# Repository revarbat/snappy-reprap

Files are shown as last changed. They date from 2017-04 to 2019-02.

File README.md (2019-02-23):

Snappy Full Rendering

Snappy-Reprap 3
===============

A parametric design for a cheap self-replicating 3D printer (reprap) that snaps together to minimize screws and non-printed parts.

Important Links:

What                 | URL
-------------------- | -------------------------------------------------------
GitHub Repository    | https://github.com/revarbat/snappy-reprap
Project Wiki         | https://github.com/revarbat/snappy-reprap/wiki/v3.0-Home
Bill of Materials    | https://github.com/revarbat/snappy-reprap/wiki/v3.0-BOM
How to Assemble      | https://github.com/revarbat/snappy-reprap/wiki/v3.0-Assembly
RepRap.org Wiki Page | http://reprap.org/wiki/Snappy
Dev Forum            | https://groups.google.com/forum/#!forum/snappy-reprap-dev



Generating STL Files
====================
For all platforms, you will need to have OpenSCAD installed. You can download OpenSCAD from their website at [http://www.openscad.org](http://www.openscad.org)

To insure the best fit of parts, print the [slop calibrator STL file](https://github.com/revarbat/snappy-reprap/blob/master/STLs/slop_calibrator_parts.stl) on the parent printer using the desired print settings. Then update the printer_slop variable in the config.scad file on line 130. Then proceed to generating STL files.

OS X:
-----
Under OS X, you'll need to make sure you have the Xcode command-line tools installed first.  You can get them by installing Xcode from the App Store.

You shouldn't need to change the Makefile.  It should set $OPENSCAD as:
```
OPENSCAD=/Applications/OpenSCAD.app/Contents/MacOS/OpenSCAD
```

To generate the STL model files, open a terminal to the snappy-reprap directory and type:
```
make
```

Linux:
------
Under Linux, you will need to edit the Makefile, and change $OPENSCAD to:
```
OPENSCAD=openscad
```
To generate the STL model files, open a terminal to the snappy-reprap directory and type:
```
make
```

Windows:
--------
Under Windows, you'll probably have to open and compile each `*_parts.scad` file individually and manually export the STL files.

You _might_ be able to run the makefile under CygWin, if you set $OPENSCAD to something like:
```
OPENSCAD="/Program Files/OpenSCAD/openscad.exe"
```

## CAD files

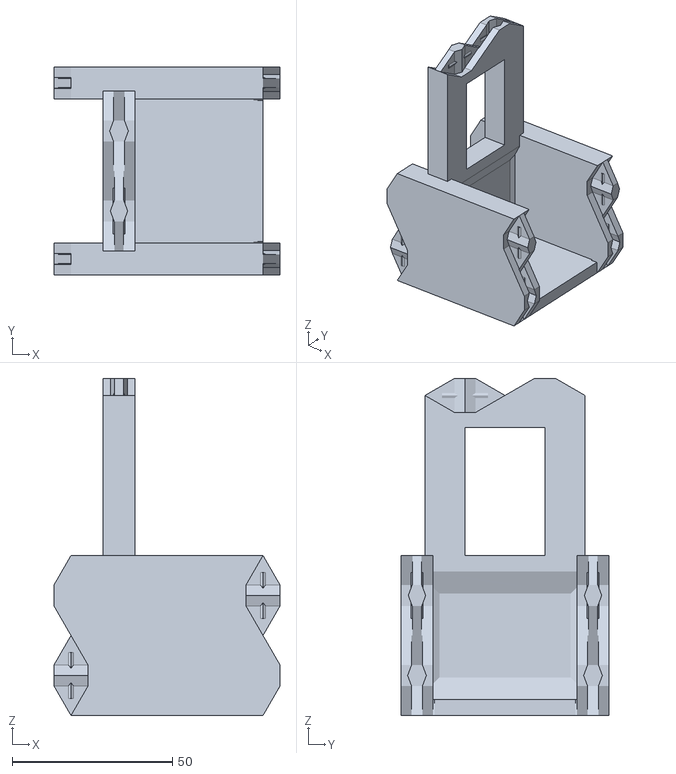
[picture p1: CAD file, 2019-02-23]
STLs/rail_z_endcap_parts.stl
70.6 x 65.0 x 105.3

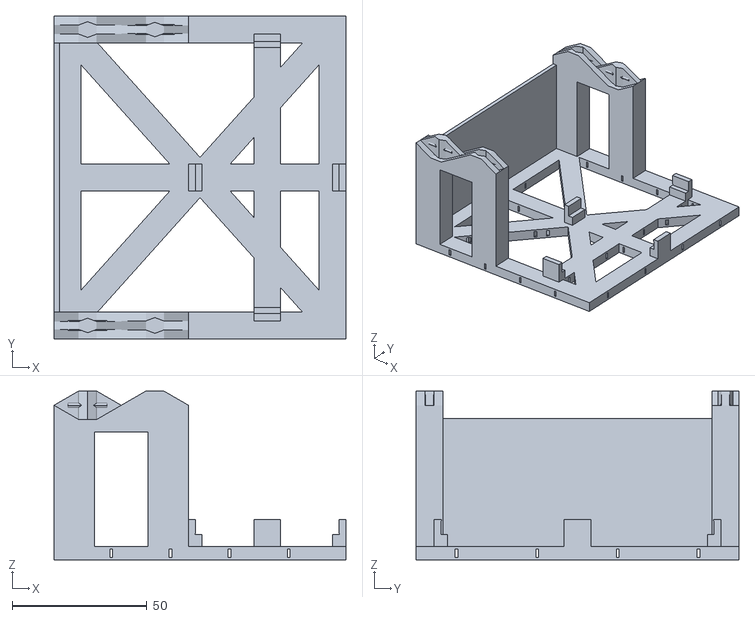
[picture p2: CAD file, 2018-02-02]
STLs/ramps_mount_parts.stl
108.5 x 120.0 x 62.8

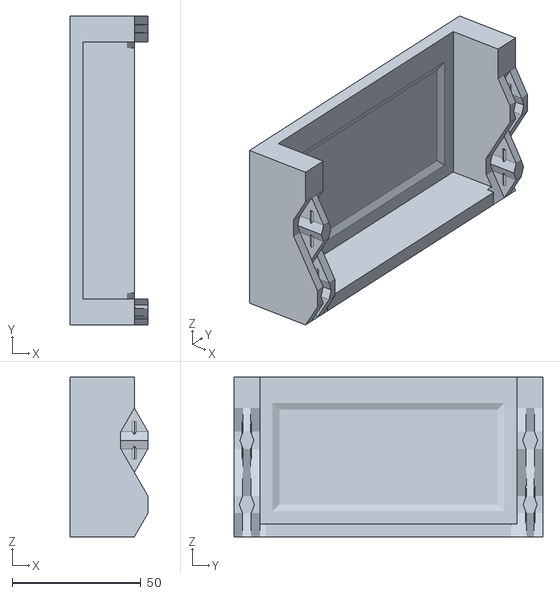
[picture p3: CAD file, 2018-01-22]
STLs/rail_y_endcap_parts.stl
30.3 x 120.0 x 62.0

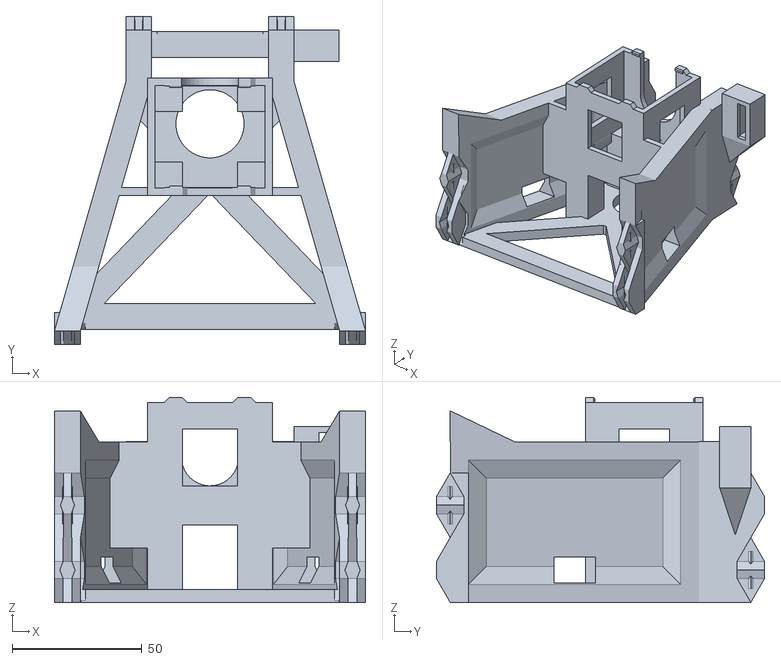
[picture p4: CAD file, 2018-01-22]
STLs/z_base_parts.stl
120.0 x 126.6 x 79.1

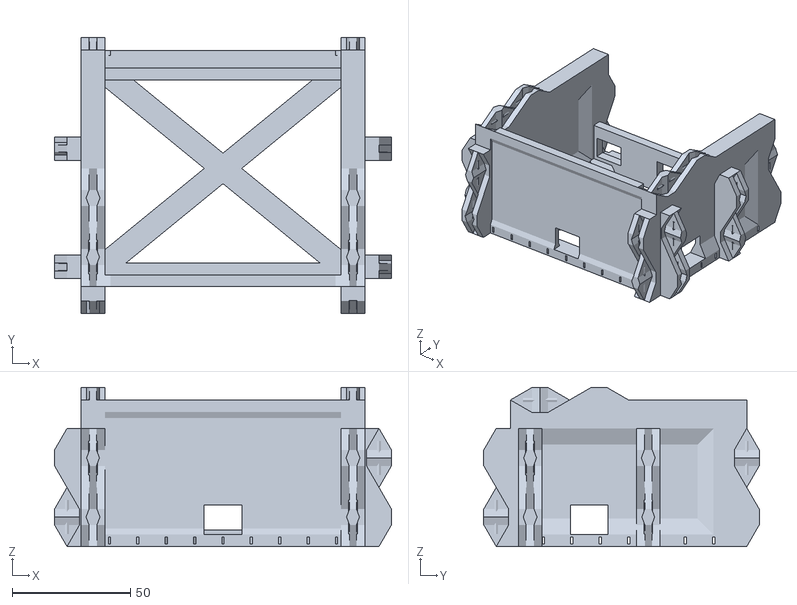
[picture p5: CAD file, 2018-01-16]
STLs/yz_joiner_parts.stl
142.6 x 116.6 x 67.3

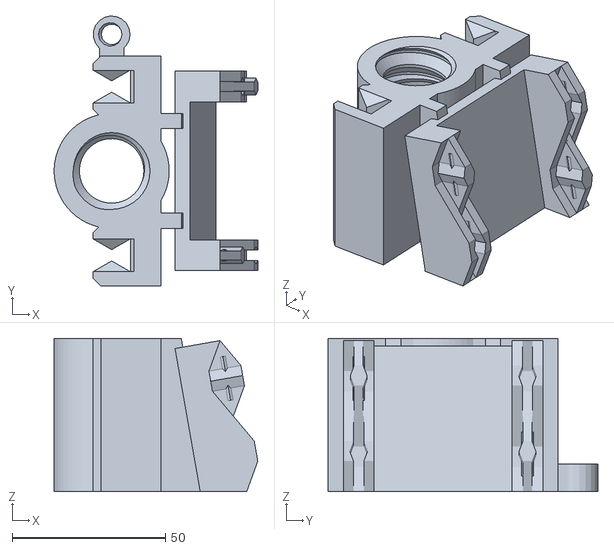
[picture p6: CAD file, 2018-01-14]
STLs/z_sled_parts.stl
66.3 x 88.0 x 50.0

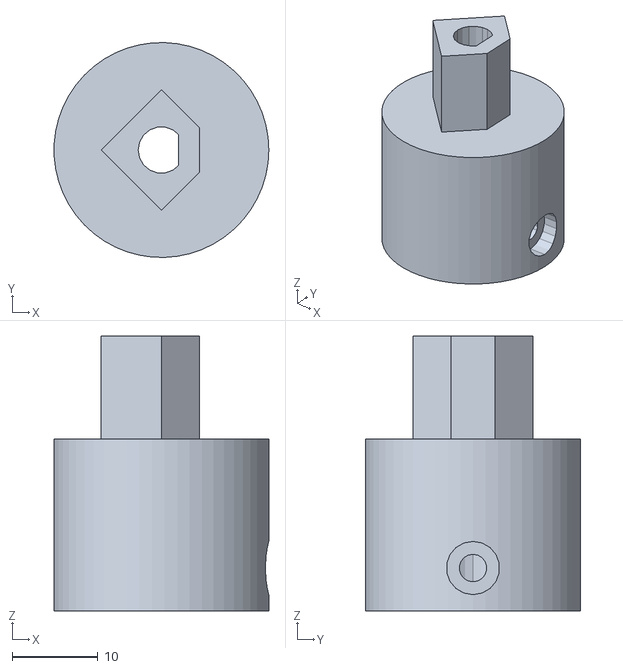
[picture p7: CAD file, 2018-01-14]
STLs/lifter_coupler_parts.stl
25.0 x 25.0 x 32.0

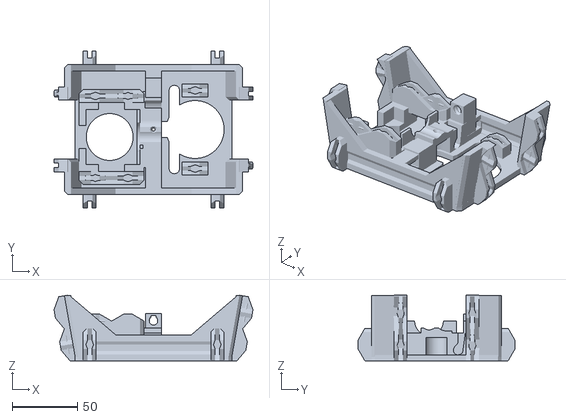
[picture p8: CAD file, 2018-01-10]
STLs/jhead_platform_parts.stl
152.8 x 120.6 x 50.5

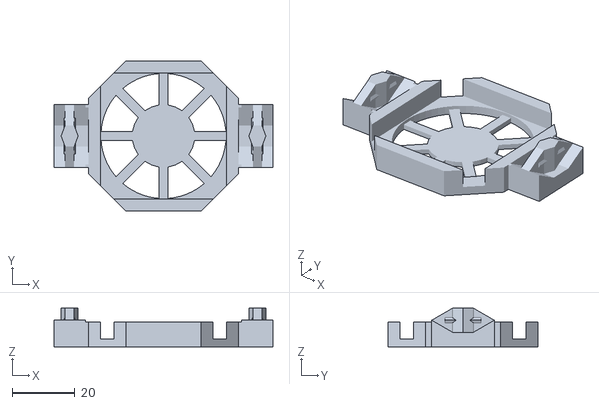
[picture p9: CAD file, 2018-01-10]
STLs/extruder_fan_clip_parts.stl
70.0 x 48.0 x 12.3

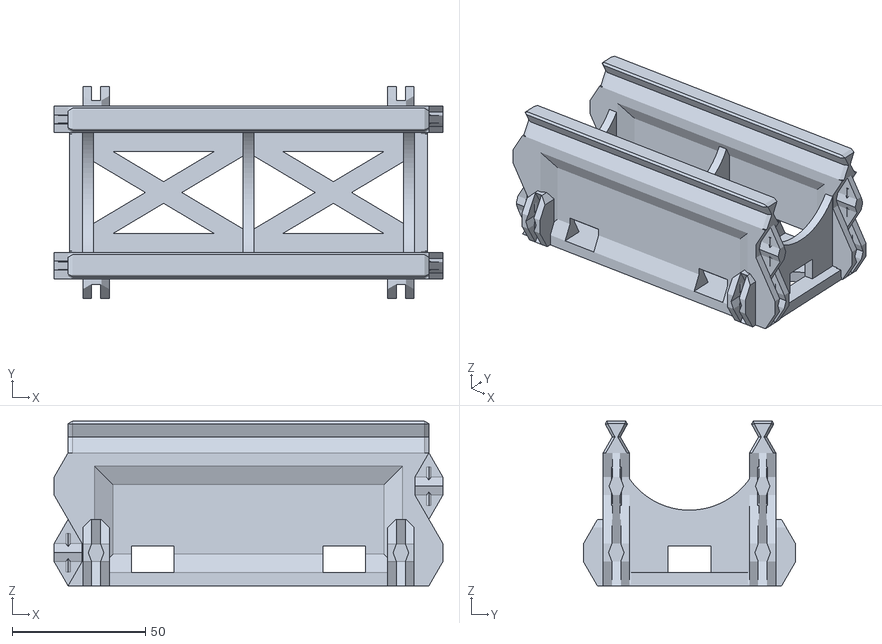
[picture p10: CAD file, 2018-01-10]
STLs/z_rail_parts.stl
146.2 x 79.8 x 62.0

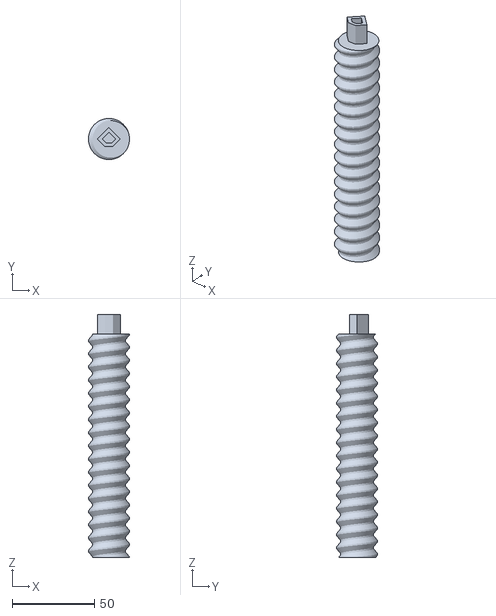
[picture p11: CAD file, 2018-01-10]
STLs/lifter_rod_parts.stl
25.0 x 25.0 x 147.8

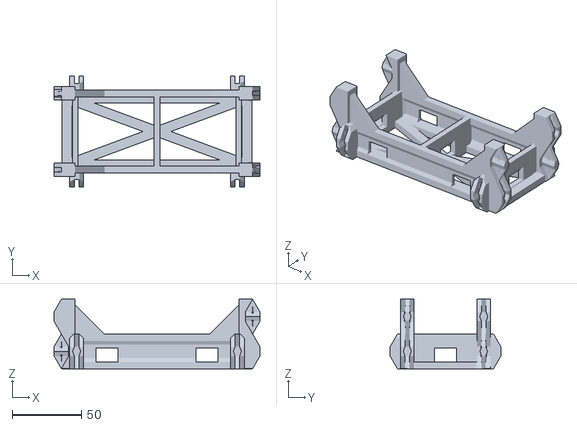
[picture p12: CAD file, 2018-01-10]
STLs/bridge_segment_parts.stl
148.3 x 79.8 x 50.0

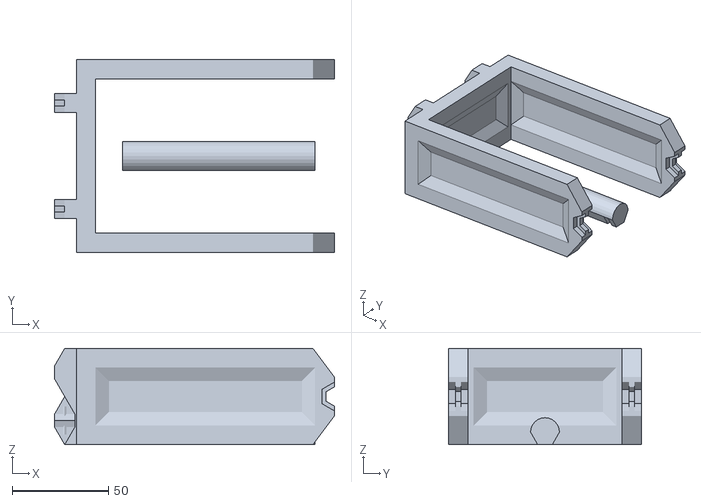
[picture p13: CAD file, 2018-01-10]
STLs/spool_holder_parts.stl
145.3 x 100.0 x 50.0

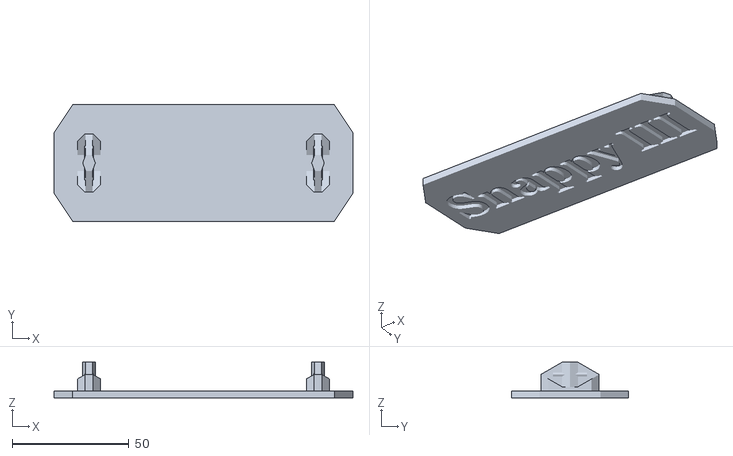
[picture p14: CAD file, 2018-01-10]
STLs/snappy_logo_parts.stl
128.0 x 50.0 x 15.3

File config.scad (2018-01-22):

snappy_version = 2.000;


// 0 = Thinning Walls (Thin in the middle, thick at edges.  Prettier smooth solid walls.)
// 1 = Corrugated closed walls. (Zig-zagged solid walls. Less shrinkage stress.)
// 2 = Crossbeam walls. (Open sparse struts. Far less shrinkage stress. Recommended.)
wall_styling = 0;


platform_length = 100.0;  // mm.  Must be a multiple of rack_tooth_size.
platform_width  = 150.0;  // mm
platform_height =  40.0;  // mm
platform_thick  =   5.0;  // mm

rail_length     = 136.0;  // mm  Should match lifter_rod_length
rail_height     =  50.0;  // mm
rail_thick      =   5.0;  // mm

motor_rail_length = 128.0; // mm

groove_angle    =  30;   // degrees
groove_height   =  12;   // mm

joiner_angle    =  30;   // degrees
joiner_width    =  10;   // mm

rack_tooth_size     = 10/3;    // mm per tooth.
rack_height         = 15;    // mm
gear_base           = 10;    // mm
gear_teeth          = 24;
set_screw_size      =  3;    // mm size of set screw in drive gears, couplers, etc
motor_length        = 39.25; // mm length of NEMA17 motor.
motor_shaft_size    =  5;    // mm diameter of NEMA17 motor shaft.
motor_shaft_length  = 20;    // mm length of exposed NEMA17 motor shaft.
motor_shaft_flatted = true;  // Is motor shaft keyed? (RECOMMENDED)

lifter_rod_diam     =  25; // mm
lifter_rod_pitch    =   8; // mm lift per revolution
lifter_rod_length   = 136; // mm. Must be a multiple of lifter_rod_pitch
lifter_rod_angle    =  50; // degrees tooth face angle
lifter_tang_length  =  12; // mm
lifter_tang_width   =   5; // mm
lifter_coupler_len  =  20; // mm

adjust_screw_diam   =  8.0; // mm
adjust_screw_pitch  =  3.0; // mm
adjust_screw_length = 30.0; // mm
adjust_screw_angle  = 50.0; // mm
adjust_screw_knob_d = 12.0; // mm
adjust_screw_knob_h =  5.0; // mm

// Mechanical endstop bare microswitch.
endstop_hole_spacing =  9.5; // mm
endstop_hole_inset   =  8.0; // mm
endstop_hole_hoff    = 10.0; // mm
endstop_click_voff   =  3.0; // mm
endstop_screw_size   =  2.5; // mm
endstop_length       = 19.8; // mm
endstop_thick        =  6.5; // mm
endstop_depth        = 10.0; // mm

// Standard Mk2b Heated Build Platform from RepRapDiscount.com
hbp_width       = 215;   // mm
hbp_length      = 215;   // mm
hbp_hole_width  = 208.5; // mm
hbp_hole_length = 208.5; // mm
hbp_screwsize   =   3;   // mm

// Standard 200mm square borosilicate glass build platform
glass_width     = 200;   // mm
glass_length    = 214;   // mm
glass_thick     =   3;   // mm
//glass_thick     =   4.6;   // mm  3mm glass and 1.6mm heated bed.  Print supports in ABS.

// Cable chain dimensions
cable_chain_height = 15;  // mm
cable_chain_width  = 25;  // mm
cable_chain_length = 26;  // mm
cable_chain_pivot  =  5;  // mm
cable_chain_bump   =  1.5;  // mm
cable_chain_wall   =  3.25;  // mm

spool_holder_length = 140.0;  // mm

bridge_arch_angle   =  10.0;  // degrees

jhead_vent_span     =  20.0;  // mm
jhead_barrel_diam   =  16.0;  // mm
jhead_shelf_thick   =   4.8;  // mm
jhead_groove_thick  =   4.6;  // mm
jhead_groove_diam   =  12.0;  // mm
jhead_cap_height    =   8.2;  // mm
jhead_cap_diam      =  12.0;  // mm

extruder_thick       =   5.0;  // mm
extruder_shaft_len   =  25.0;  // mm
extruder_drive_diam  =  12.5;  // mm

/*
// 626 bearing
extruder_idler_diam  =  19.0;  // mm
extruder_idler_axle  =   6.0;  // mm
extruder_idler_width =   6.0;  // mm
*/

/*
// SAE bearing 5/8"OD x 1/4"ID x 1/5"W
extruder_idler_diam  =  15.9;  // mm
extruder_idler_axle  =   6.3;  // mm
extruder_idler_width =   5.0;  // mm
*/

// 686 bearing
extruder_idler_diam  =  13.0;  // mm
extruder_idler_axle  =   6.0;  // mm
extruder_idler_width =   5.0;  // mm

extruder_fan_size    =  40.0;  // mm
extruder_fan_thick   =  10.0;  // mm

cooling_fan_size     =  40.0;  // mm
cooling_fan_thick    =  10.0;  // mm
cooling_duct_height  =  18.0;  // mm

filament_diam        =   1.75; // mm

// This is the slop needed to make parts fit more exactly, and might be
// printer and slicer dependant.  Printing a slop calibration block should
// help dial this setting in for your printer.
printer_slop = 0.20;  // mm
gear_backlash = 0;  // mm



// Commonly used derived values.  Don't change these.
pi = 3.141592653589793236+0.0;
extruder_length = motor_rail_length;
shaft_clear = max(0, motor_shaft_length - (rack_height + gear_base));
rail_offset = shaft_clear + platform_thick + rack_height/2 + 2.0;
rail_spacing = platform_width - joiner_width*4 - 10;
rail_width = rail_spacing + joiner_width*2;
rack_base = rail_offset - platform_thick + groove_height/2 - rack_height;
motor_mount_spacing = 43 + joiner_width + 10;
side_mount_spacing = motor_rail_length - 10*2;
platform_z = rail_height + groove_height + rail_offset;
cantilever_length = (motor_rail_length + 2*platform_length - 2*rail_height - extruder_length - groove_height)/2;
motor_top_z = rail_height + groove_height - rack_height/2 - gear_base - 2;
lifter_tooth_depth = lifter_rod_pitch / 3.2;
z_joiner_spacing = lifter_rod_diam + 20 + joiner_width;
z_base_height = 2*platform_z + glass_thick + 12 + 10 - rail_height - groove_height;
adjust_thread_depth = adjust_screw_pitch/3.2;
drive_gear_diam = (gear_teeth+2)*rack_tooth_size/pi;

wall_styles = ["thinwall", "corrugated", "crossbeams"];
wall_style = wall_styles[wall_styling];


// vim: noexpandtab tabstop=4 shiftwidth=4 softtabstop=4 nowrap

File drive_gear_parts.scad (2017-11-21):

include <config.scad>
use <GDMUtils.scad>
use <publicDomainGearV1.1.scad>


$fa = 2;
$fs = 2;

module drive_gear() {
	shaft = motor_shaft_size;
	rack_module = rack_tooth_size / pi;
	gear_pcd = gear_teeth * rack_module;
	addendum = rack_module;
	dedendum = rack_module * 1.25;
	gear_id = gear_pcd - 2*dedendum;
	gear_od = gear_pcd + 2*addendum;
	CA = 30;
	twist = 360*0.5*rack_height*tan(CA) / (gear_pcd * pi);
	base = gear_base - 1;

	color("Salmon")
	prerender(convexity=10)
	difference() {
		union() {
			up(base+rack_height/2-0.05) {
				difference() {
					// Herringbone gear
					zflip_copy() {
						up(rack_height/2/2) {
							gear (
								mm_per_tooth    = rack_tooth_size,
								number_of_teeth = gear_teeth,
								thickness       = rack_height/2,
								hole_diameter   = shaft/2,
								twist           = twist,
								teeth_to_hide   = 0,
								pressure_angle  = 20,
								backlash        = gear_backlash
							);
						}
					}

					// Bevel end of gear.
					up(rack_height/2) {
						zflip() {
							difference() {
								down(0.01) cylinder(h=1, d=gear_od+2, center=false);
								cylinder(h=1, d1=gear_id, d2=gear_od, center=false);
							}
						}
					}
				}
			}

			up(base/2) {
				difference() {
					// Gear Base
					cylinder(h=base, d=max(18,gear_od), center=true);

					right(motor_shaft_size/2+1.5) {
						yrot(90) {
							// Nut Slot
							scale([1.1, 1.04, 1.04]) hull() {
								metric_nut(size=set_screw_size, hole=false);
								right(base/2) metric_nut(size=set_screw_size, hole=false);
							}

							// Set screw hole.
							down(4) cylinder(d=set_screw_size+printer_slop, h=30, $fn=18);

							// Screw head clearance
							up(6) cylinder(d=set_screw_size*2+printer_slop, h=30, $fn=18);
						}
					}
				}
			}
		}


		down(0.01) {
			difference() {
				union() {
					// Shaft hole
					cylinder(h=rack_height+base, d=shaft, center=false, $fn=18);

					// chamfer bottom of shaft hole.
					down(0.01) {
						cylinder(h=2, d1=shaft+2, d2=shaft, center=false, $fn=18);
					}
				}

				// Shaft flat side.
				if (motor_shaft_flatted) {
					right(1.4*shaft)
						cube(size=[shaft*2, shaft*2, (rack_height+base)*3], center=true);
				}
			}
		}
	}
}
//!drive_gear();


module drive_gear_parts() { // make me
	drive_gear();
}



drive_gear_parts();



// vim: noexpandtab tabstop=4 shiftwidth=4 softtabstop=4 nowrap

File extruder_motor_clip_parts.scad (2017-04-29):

include <config.scad>
use <GDMUtils.scad>
use <NEMA.scad>
use <joiners.scad>


$fa = 2;
$fs = 2;

thick = 6;
motor_width = nema_motor_width(17);


module extruder_motor_clip()
{
	color("Turquoise")
	prerender(convexity=10)
	difference() {
		union() {
			up(motor_width/2+5+thick/2) {
				cube(size=[motor_mount_spacing+joiner_width, rail_height, thick], center=true);
				xspread(motor_width) {
					yspread(motor_length-5) {
						down(15/2) {
							cube([15,15,15], center=true);
						}
					}
				}
			}

			// Joiners
			xrot(-90) joiner_pair(spacing=motor_mount_spacing, h=rail_height, w=joiner_width, l=motor_width/2+5+1, a=joiner_angle);
		}

		// Clear for motor.
		cube([motor_width+printer_slop, motor_length+printer_slop, motor_width], center=true);

		// Ventilation hole
		cylinder(h=100, d=motor_width*0.75, center=true);

		// chamfer edges
		xspread(motor_mount_spacing+joiner_width) {
			yspread(rail_height) {
				chamfer_mask_z(l=rail_height*2, chamfer=joiner_width/3);
			}
		}
	}
}
//!extruder_motor_clip();



module extruder_motor_clip_parts() { // make me
	up(motor_width/2+5+6/2) {
		zrot(90) yrot(180) extruder_motor_clip();
	}
}



extruder_motor_clip_parts();


// vim: noexpandtab tabstop=4 shiftwidth=4 softtabstop=4 nowrap

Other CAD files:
STLs/rambo_mount_parts.stl
STLs/cable_chain_link_parts.stl
STLs/rail_segment_parts.stl
STLs/drive_gear_parts.stl
rail_motor_segment_parts.scad
GDMUtils.scad
NEMA.scad
STLs/adjustment_screw_parts.stl
STLs/bridge_brace_center_parts.stl
STLs/bridge_brace_parts.stl
STLs/build_platform_support_parts.stl
STLs/cable_chain_mount_parts.stl
STLs/compression_screw_parts.stl
STLs/cooling_fan_shroud_parts.stl
STLs/extruder_fan_shroud_parts.stl
STLs/extruder_idler_parts.stl
STLs/extruder_motor_clip_parts.stl
STLs/fan_clip_parts.stl
STLs/glass_bed_support_parts.stl
STLs/heated_bed_support_parts.stl
STLs/rail_motor_segment_parts.stl
STLs/rail_xy_motor_segment_parts.stl
STLs/rrd_graphic_lcd_base_parts.stl
STLs/rrd_graphic_lcd_cover_parts.stl
STLs/sled_endcap_parts.stl
STLs/sled_parts.stl
STLs/slop_calibrator_parts.stl
STLs/support_leg_parts.stl
STLs/wire_clip_parts.stl
STLs/xy_joiner_parts.stl
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

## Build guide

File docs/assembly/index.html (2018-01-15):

# Snappy RepRap Assembly Instructions

## XY Motor Assembly

### Step 1

  - Print a drive gear with high (around 50%) infill density. Insert a 3mm nut into the slot on the bottom of the drive gear. Push it down the slot until the holes line up with the hole in the nut.

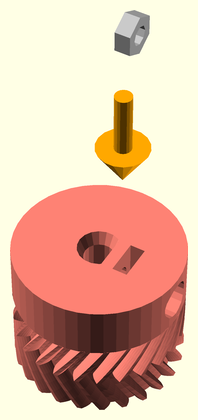
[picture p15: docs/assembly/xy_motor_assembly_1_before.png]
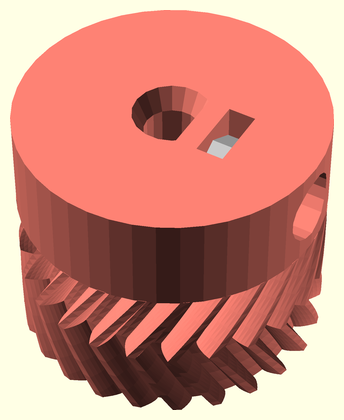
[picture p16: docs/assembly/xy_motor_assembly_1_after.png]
 |  | 

### Step 2

  - Thread a 3mm diam (12mm long) bolt just through the inserted nut.

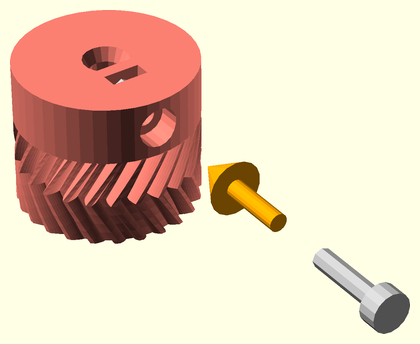
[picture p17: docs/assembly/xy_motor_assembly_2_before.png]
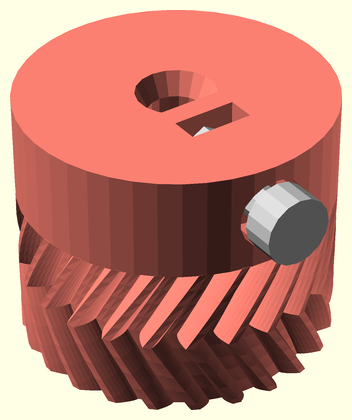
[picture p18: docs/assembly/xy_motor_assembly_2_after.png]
 |  | 

### Step 3

  - Slide a drive gear onto the shaft of a stepper motor, making sure to align the flat of the shaft with the flat of the shaft hole. Tighten the set screw onto the shaft flat. Repeat this with the other drive gear and another stepper. Lubricate the drive gear teeth with mineral oil.

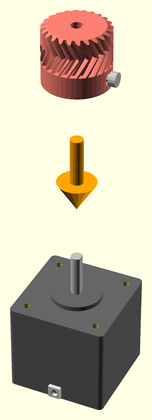
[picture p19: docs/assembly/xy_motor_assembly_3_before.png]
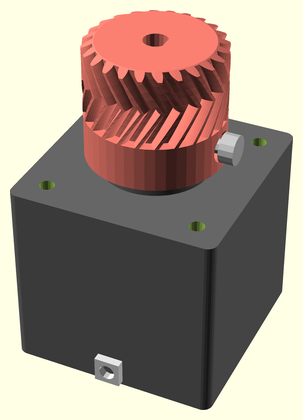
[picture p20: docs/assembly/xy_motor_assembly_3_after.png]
 |  | 

## Y Motor Segment Assembly

### Step 1

  - Seat the stepper motor with drive gear in the X/Y motor rail segment, with the wiring facing towards the left. Route the wiring out the front left wiring access hole.

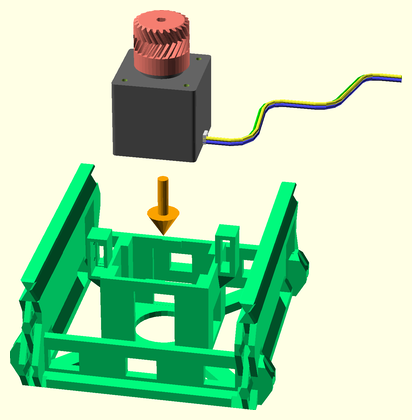
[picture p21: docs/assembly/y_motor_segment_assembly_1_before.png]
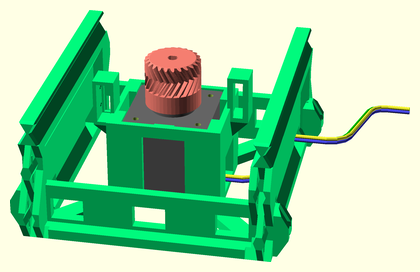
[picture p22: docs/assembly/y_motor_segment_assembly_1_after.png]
 |  | 

### Step 2

  - Insert the limit microswitch in the left-side limit switch clip in the X/Y motor rail segment. Orient the switch with the arm leaning outwards on top. Route the wiring through the back of the limit switch clip, and out the same front-left wiring access hole as the motor wires.

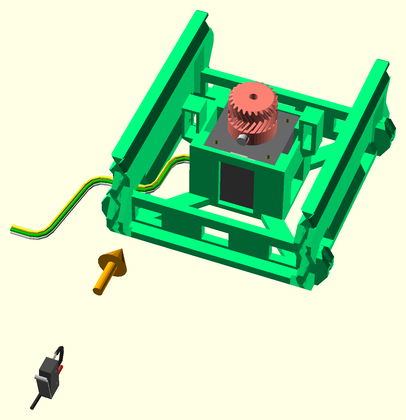
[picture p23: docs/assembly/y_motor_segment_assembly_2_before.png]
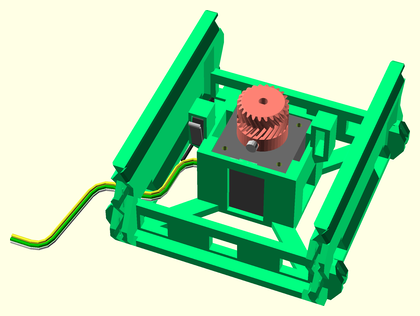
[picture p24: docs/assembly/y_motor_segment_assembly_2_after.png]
 |  | 

## Y Axis Assembly

### Step 1

  - Join a rail segment to each end of another motor rail assembly. Apply mineral oil to the slider rail V-grooves for lubrication.

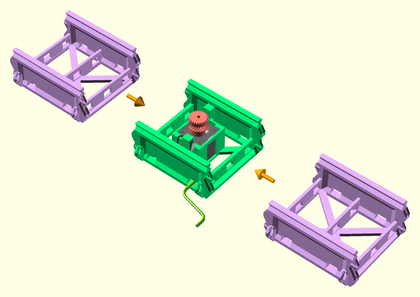
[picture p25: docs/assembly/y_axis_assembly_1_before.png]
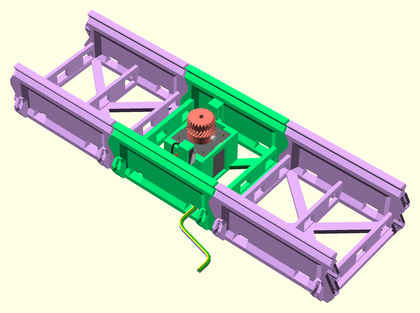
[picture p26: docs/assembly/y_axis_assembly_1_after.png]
 |  | 

### Step 2

  - Join opposing glass bed supports to either side of both Y sled endcaps. Screw an adjustment screws into each of the supports, leaving them loose for now.

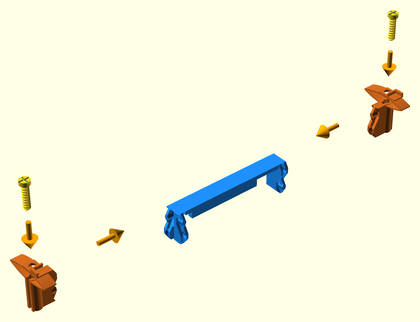
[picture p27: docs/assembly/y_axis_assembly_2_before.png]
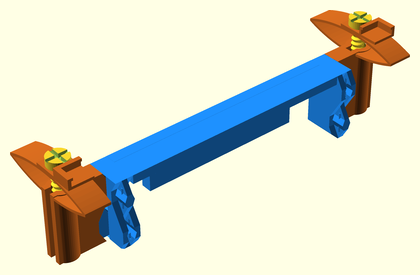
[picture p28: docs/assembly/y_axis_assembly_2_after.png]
 |  | 

### Step 3

  - Join two XY sled parts together. Make sure the bottom racks line up. Lubricate the slider pinchers and gear rack teeth on the underside of the sled with mineral oil.

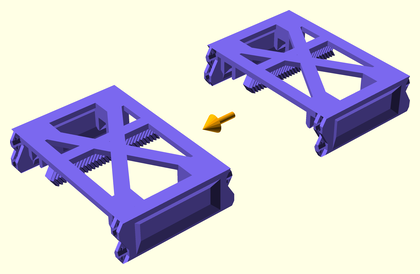
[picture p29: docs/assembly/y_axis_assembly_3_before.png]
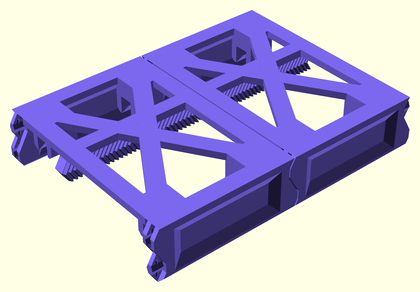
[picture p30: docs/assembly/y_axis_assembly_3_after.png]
 |  | 

### Step 4

  - Join a Y sled endcap assembly to one end of the Y sled central assembly.

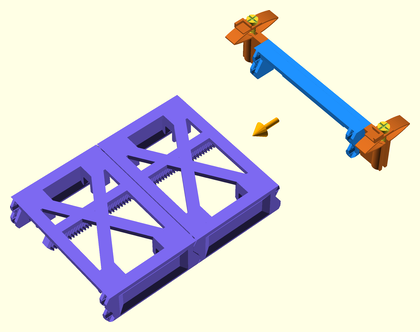
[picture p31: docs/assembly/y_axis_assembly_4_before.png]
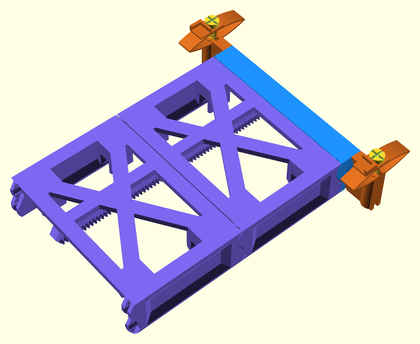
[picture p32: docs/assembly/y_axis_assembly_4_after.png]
 |  | 

### Step 5

  - Slide the Y sled partial assembly onto the Y axis rails assembly, so that it is centered. The gear rack should slide between the limit switch on the left, and the drive gear. Adjust the drive gear if necessary, so that it aligns exactly with the herringbone rack.

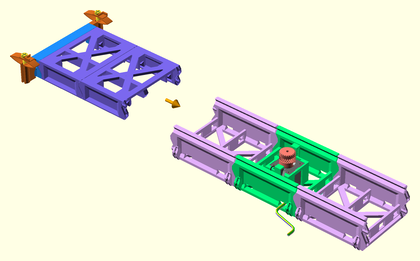
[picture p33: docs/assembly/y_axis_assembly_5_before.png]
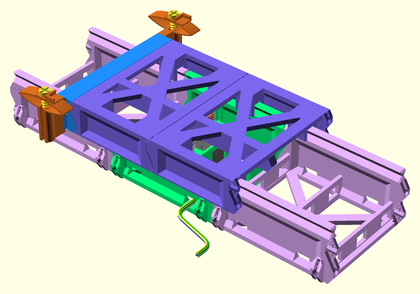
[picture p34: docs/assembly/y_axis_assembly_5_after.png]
 |  | 

### Step 6

  - Join the other Y sled endcap assembly to the end of the Y sled partial assembly.

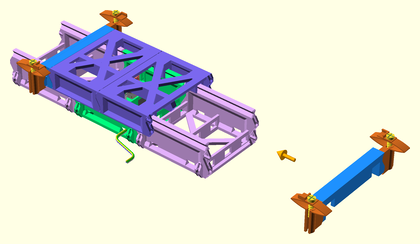
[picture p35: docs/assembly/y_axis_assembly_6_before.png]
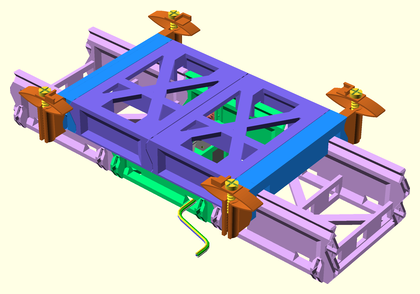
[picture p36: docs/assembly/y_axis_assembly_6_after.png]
 |  | 

### Step 7

  - Optionally join a rail endcap to each end of the Y axis.

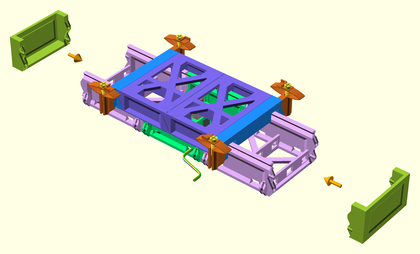
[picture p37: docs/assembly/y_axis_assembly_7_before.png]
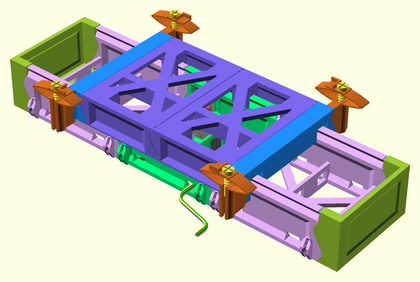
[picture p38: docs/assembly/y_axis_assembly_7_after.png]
 |  | 

## X Motor Segment Assembly

### Step 1

  - Seat the stepper motor with drive gear in the X/Y motor rail segment, with the wiring facing towards the left. Route the wiring out the front left wiring access hole.

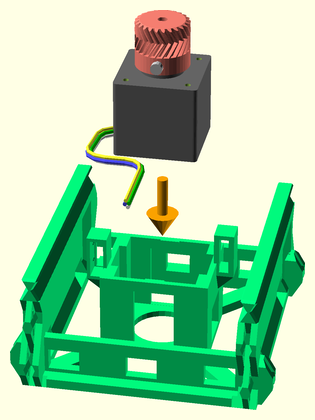
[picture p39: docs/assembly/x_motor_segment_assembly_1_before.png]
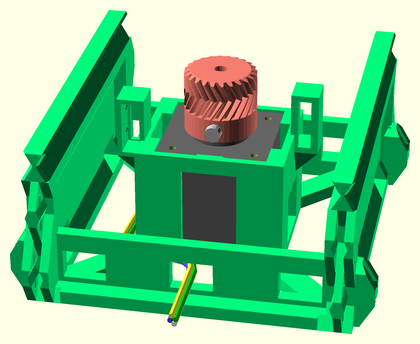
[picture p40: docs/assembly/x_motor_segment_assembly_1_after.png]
 |  | 

### Step 2

  - Insert the limit microswitch in the left-side limit switch clip in the X/Y motor rail segment. Route the wiring through the back of the limit switch clip, and out the same front-left wiring access hole as the motor wires.

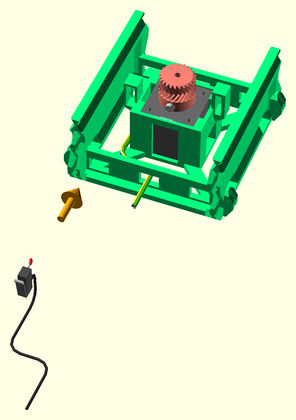
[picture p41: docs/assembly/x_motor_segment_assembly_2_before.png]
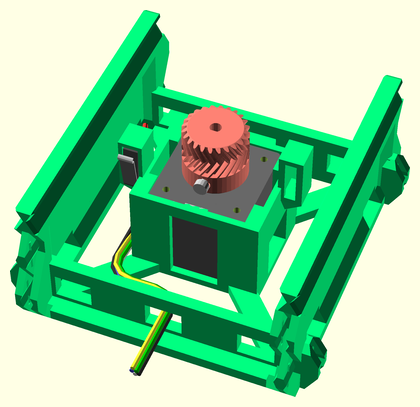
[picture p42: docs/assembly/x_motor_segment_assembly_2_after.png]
 |  | 

## X Axis Assembly

### Step 1

  - Join a rail segment to each end of a motor rail assembly, to make the X axis slider. Route the wiring to one end of the slider assembly. Apply mineral oil to the slider rail V-grooves for lubrication.

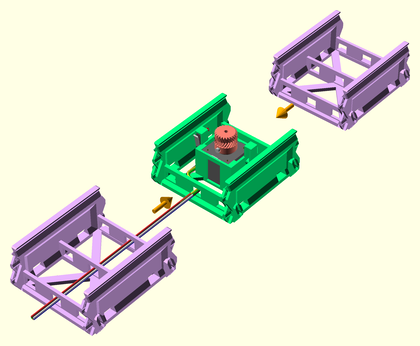
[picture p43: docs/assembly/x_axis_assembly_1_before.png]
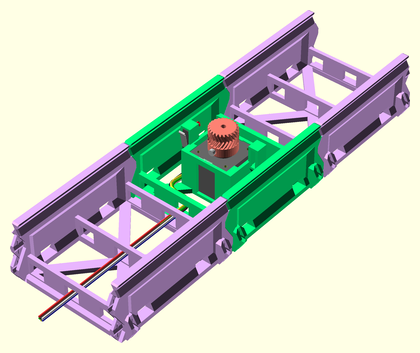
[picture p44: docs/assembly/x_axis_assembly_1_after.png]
 |  | 

### Step 2

  - Join two XY sled parts together. Make sure the bottom racks line up. Lubricate the slider pinchers and gear rack teeth on the underside of the sled with mineral oil.

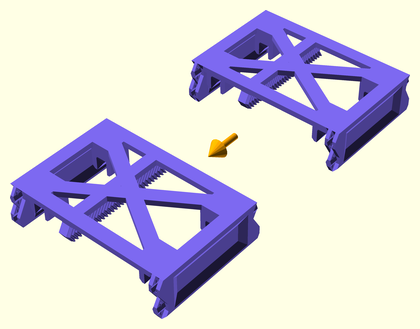
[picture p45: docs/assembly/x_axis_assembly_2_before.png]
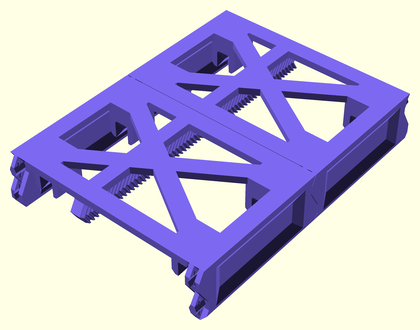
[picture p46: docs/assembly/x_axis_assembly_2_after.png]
 |  | 

### Step 3

  - Join the X sled cable-chain mount to the front/left side of the X sled endstop.

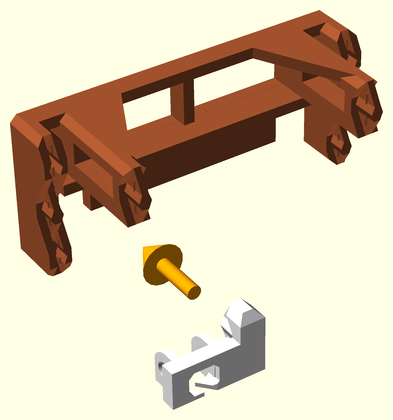
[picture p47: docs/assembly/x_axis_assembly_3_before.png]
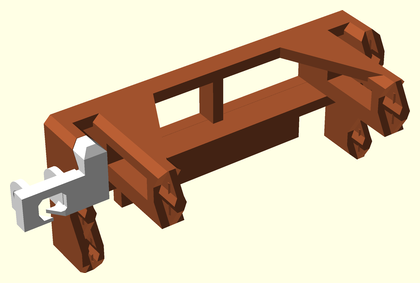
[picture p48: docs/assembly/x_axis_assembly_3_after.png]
 |  | 

### Step 4

  - Join an X-Y joiner endcap to one end of the X sled central assembly.

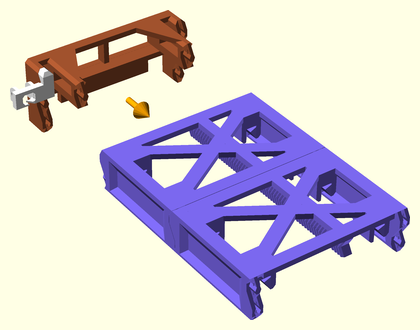
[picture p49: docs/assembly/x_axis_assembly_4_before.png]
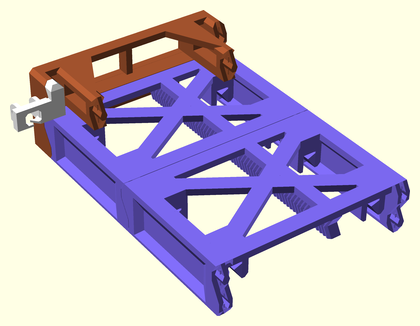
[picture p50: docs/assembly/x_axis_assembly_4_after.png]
 |  | 

### Step 5

  - Slide the X sled partial assembly onto the X axis rails assembly, so that it is centered.

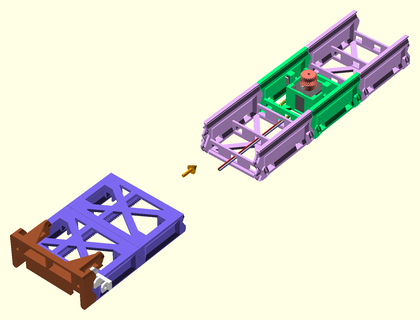
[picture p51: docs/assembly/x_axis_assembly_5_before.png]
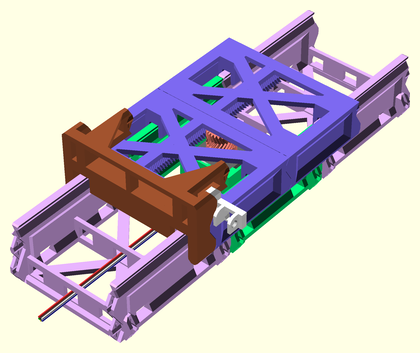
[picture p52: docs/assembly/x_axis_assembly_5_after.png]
 |  | 

### Step 6

  - Connect the Y axis assembly to the XY joiner on the X axis partial assembly. Route the Y axis wiring through the front hole in the XY joiner.

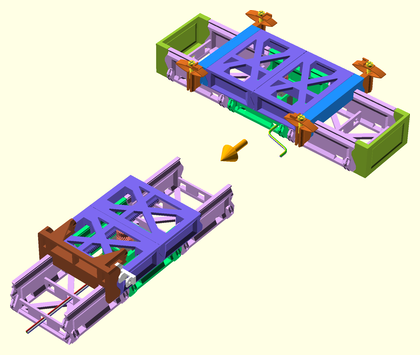
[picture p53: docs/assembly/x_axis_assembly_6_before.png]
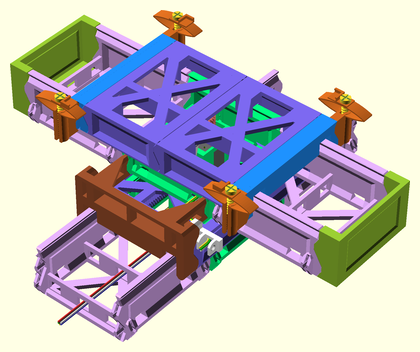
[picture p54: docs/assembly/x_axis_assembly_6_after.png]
 |  | 

### Step 7

  - Join the other X sled endcap assembly to the end of the X sled assembly, fixing the Y sled assembly in place.

 |  | 

### Step 8

  - Attach the cable chain joiner mount to the X motor segment, on the same side as the X sled cable chain joiner and Y axis wiring.

 |  | 

### Step 9

  - Attach the cable-chain assembly (with 13 or 14 links) to the cable chain mounts on the X axis assembly, making sure to feed the Y-axis wiring through the cable chain. Route the wiring in through the wiring access hole beside the cable chain mount, then out through the end of the X axis assembly. You may need to lubricate each cable-chain pivot with mineral oil.

 |  | 

## Lifter Assembly

### Step 1

  - Press fit a nut into slot on the bottom of lifter coupler. Press into slot until it reaches the bottom.

 |  | 

### Step 2

  - Thread a 3mm x 12mm screw just barely through the nut in the screwhole.

 |  | 

### Step 3

  - Press fit the lifter rod fully onto the top of the coupler. If it's loose at all, superglue them carefully together.

 |  | 

### Step 4

  - Press fit another lifter rod fully onto the top of the lifter assembly. Superglue it carefully if it is at all loose.

 |  | 

### Step 5

  - Press fit the lifter rod assembly onto the stepper motor shaft, making sure the set screw is on the flatted side of the shaft. Tighten the set screw firmly. Apply mineral oil to the screw rod threads for lubrication.

 |  | 

## Z Tower Assembly

### Step 1

  - Attach two Z rail segments together to make a Z tower rail assembly. Do this again to make a second tower. Superglue these together if they aren't attached firmly. Lubricate the slider rails and lifter screw slots with mineral oil.

 |  | 

### Step 2

  - Attach support legs to each side of a YZ Joiner part. Do this again for a second YZ Joiner part.

 |  | 

### Step 3

  - Attach a Z base part to the top of each YZ joiner assembly, to make two tower base assemblies. Superglue these together if the attachment is wobbly in any way.

 |  | 

### Step 4

  - Insert a microswitch into the tower base assembly. Route the wiring down to the base of the tower.

 |  | 

### Step 5

  - Attach a Z tower rail assembly to the top of each tower base assembly. Superglue these together if the attachment is wobbly in any way.

 |  | 

### Step 6

  - Slide the lifter assembly (motor and lifter rods) into the motor mount on the Z base segment of the tower assembly.

 |  | 

### Step 7

  - Attach a cable chain joiner mount to the front-size of the left Z tower, above the top hole of the bottom rail segment.

 |  | 

## Extruder Assembly

### Step 1

  - Insert the 686 bearing into the extruder idler arm.

 |  | 

### Step 2

  - Insert the idler axle through the 686 bearing, and lock it into the extruder idler arm with the axle clip.

 |  | 

### Step 3

  - Attach the extruder drive gear onto the stepper motor shaft.

 |  | 

### Step 4

  - Slide the JHead extruder hot end into the slot in the bottom of the JHead platform. Route the wiring up through the wiring access slot, and along the back of the extruder platform.

 |  | 

### Step 5

  - Clip the extruder motor with drive gear to the jhead platform using the extruder motor clip.

 |  | 

### Step 6

  - Insert the idler arm into the idler hinge hole on the JHead platform.

 |  | 

### Step 7

  - Insert the idler latch arm into the latch hinge hole on the JHead platform.

 |  | 

### Step 8

  - Insert the extruder fan shroud into the JHead platform, latching the JHead hot end, and idler and latch arms into place.

 |  | 

### Step 9

  - Clip a cooling fan to the top of the extruder fan shroud using the extruder fan clip. Route the wiring along the back side of the extruder platform. WARNING: This fan MUST be running any time the J-Head hotend is hot, or else the bottom of the mount will warp! Either hook it up to a constant 12V supply, or make sure your firmware turns it on when the extruder is hot.

 |  | 

### Step 10

  - Attach a cooling fan to the cooling fan shroud.

 |  | 

### Step 11

  - Attach the cooling fan shroud assembly to the bottom of the extruder fan shroud. Route the wiring up through the wiring access slot, and along the back side of the extruder platform.

 |  | 

## Bridge Assembly

### Step 1

  - Attach bridge segments to either end of the extruder platform assembly. Superglue these together if the attachments are in any way wobbly. Route the wiring through the left side bridge segment, and out the front-left wiring access hole.

 |  | 

### Step 2

  - Attach a vertical cable-chain mount to the front left side of the extruder bridge.

 |  | 

### Step 3

  - Thread an adjustment screw into the limit switch adjuster socket of a Z sled part. Do this again for another Z sled.

 |  | 

### Step 4

  - Attach Z sled segments to either end of the extruder bridge assembly. Superglue these on if the attachments are in any way wobbly.

 |  | 

## Top Brace Assembly

### Step 1

  - Attach a bridge side brace onto either side of a bridge center brace.

 |  | 

### Step 2

  - Attach a Z rail endstop onto either side of the bridge brace assembly.

 |  | 

## Final Assembly

### Step 1

  - Attach the right Z tower assembly to the right end of the XY axes assembly. Route the right tower wiring through the rear X axis wiring access holes.

 |  | 

### Step 2

  - Attach the left Z tower assembly to the left end of the XY axes assembly. Route all wiring out the back of the left Z tower base.

 |  | 

### Step 3

  - Lower the extruder bridge down into the Z tower grooves, screwing the lifter screws into the Z-rail racks evenly.

 |  | 

### Step 4

  - Attach the bridge brace assembly onto the top of both towers. Route each limit switch's wiring down through the wiring access holes in their respective Z tower, and out the back of the base of the left tower with the other wiring.

 |  | 

### Step 5

  - Attach a cable chain (18 links) from the extruder bridge cable chain mount to the left Z tower cable chain mount. Route the extruder bridge wiring up through the cable chain, back into the left Z tower through the wiring access hole below the cable chain mount, down the left Z tower, and back out the motor rail segment to where the controller board will be mounted. You may need to lubricate each cable-chain pivot with mineral oil.

 |  | 

### Step 6

  - Attach the spool holder to the top of the right Z tower.

 |  | 

### Step 7

  - Attach the RAMPS motherboard mount to the end of the printer base.

 |  | 

### Step 8

  - Lower the glass build platform into the support corner clips on the Y sled. You should be able to carefully work the clips around the glass plate's corners.

 |  | 

### Step 9

  - Cradle the spool axle in the spool holder top.

 |  | 

### Step 10

  - Optionally clean up wiring using the wiring clips.

 |  | 

## RAMPS Wiring

12. Heres a diagram of what needs to be connected where on a RAMPS 1.4 controller board.
  
  Click on the image to enlarge.

## Marlin Firmware for RAMPS

13. You can find Marlin firmware pre-configured for the Snappy with a RAMPS 1.4 controller at https://github.com/revarbat/snappy-reprap/tree/v3.0/firmware

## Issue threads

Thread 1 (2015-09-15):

BOM missing z-screw?

andrewcaustralia, 2015-09-15:
Just noticed it wasn't listed; it appears you're using a separate z-screw however am I right to assume a fixed screw stepper would also be suitable? IE - http://imgur.com/2MpQk3C

revarbat, 2015-09-18:
The lifter rods are only really needed for the v0.95 version of the printer.  I recommend a large thread size, though, so the z_sled parts man interface with them cleaner.

andrewcaustralia, 2015-09-18:
Ah I get it now; was looking at the original pictures and trying to understand how they worked :-) :+1:

Closed 2015-09-18.

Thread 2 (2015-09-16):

Documentation missing parts sizes

ArktekniK, 2015-09-16:
Hi,

Having a look through the repo I can't seem to find details on the minimum bed size needed to print these parts?

Assuming the STLs are in mm scale, it looks like the rail_segment_parts (for example) is too large to print on a Printrbot Simple Metal with a bed of 152x152x152mm.

andrewcaustralia, 2015-09-16:
The longest piece is the "rail_segment_parts.stl" which is 160.58 x 134.58 x 61.50mm
The tallest piece is the "z_joiner_parts.stl" which is 150.05 x 56.29 x 110.00mm

jkeegan, 2015-09-16:
Yeah unfortunately *my* Prusa IT2 (might be different for others based on extruder) can only print up to about 65mm tall before hitting the bars, which is the main reason I'm thinking of making a 3rd printer. The thing I dislike about the Prusa i3 is the frame - a large vitamin. The thing I dislike about the Taz is extruded aluminum rails - vitamins that you can't buy at your local hardware store or make easily in some 3rd-world country. This however is very tempting. Any idea *how many* of the objects are taller than 60-65mm? (I could see printing a few of the parts on someone else's printer and treat those first copies as vitamins and still count it as my RepRap printing it)..

ezrec, 2015-09-16:
I have a 180mm diameter Delta, but only printable to about 150mm diameter, so I'm going to have to scale-in-Y down a bit when I start printing these.

When I get to that point, I'll start a fork with SCAD files adjusted to the smaller size.

(Working on consistent bed adhesion at the moment and stringiness issues at the moment...)

ArktekniK, 2015-09-16:
I also thought about rescaling the parts but decided it is not a good idea because several parts interface/lock with motors, board mounts etc. Therefore I'm now at the point where I'll probably fork and modify the scad for the problematic parts.

@revarbat If I make suitable changes and submit a pull request would that be okay?

revarbat, 2015-09-17:
Here's the current part sizes.

part name                              | size
---------------------------------------|------------------------
cable_chain_link_parts.stl    | 142.0 x 137.0 x  13.0
cable_chain_mount_parts.stl  |   93.5 x  89.5 x  25.0
cooling_fan_shroud_parts.stl  |  84.0 x  44.1 x  19.1
drive_gear_parts.stl          |  47.9 x  48.0 x  20.0
extruder_fan_clip_parts.stl    | 70.0 x  48.0 x  12.3
extruder_fan_shroud_parts.stl |  50.0 x  48.0 x  39.7
extruder_idler_parts.stl      |  67.9 x  51.9 x  36.0
extruder_motor_clip_parts.stl  | 50.0 x  73.0 x  37.4
jhead_platform_parts.stl     |  120.0 x 140.5 x  60.0
motor_mount_plate_parts.stl   |  92.3 x  50.0 x  26.9
platform_support_parts.stl     | 70.0 x 123.0 x  43.0
rail_endcap_parts.stl        |   35.3 x 120.0 x  62.0
rail_motor_segment_parts.stl |  110.6 x 120.0 x  62.0
rail_segment_parts.stl       |  134.6 x 160.6 x  62.0
rambo_mount_parts.stl      |    120.0 x 165.0 x  55.8
ramps_mount_parts.stl       |   120.0 x 111.5 x  65.8
sled_endcap_parts.stl        |  157.7 x  23.8 x  40.0
sled_parts.stl               |  107.7 x 150.0 x  40.0
slop_calibrator_parts.stl    |   67.0 x 100.0 x  15.0
spool_holder_parts.stl       |  120.0 x 155.3 x  62.0
support_leg_parts.stl         |  60.0 x  88.2 x  50.0
xy_joiner_parts.stl           |  65.0 x 150.0 x  53.3
yz_joiner_parts.stl         |   142.6 x 116.6 x  67.3
z_joiner_parts.stl          |   150.1 x  56.3 x 110.0

Two parts exceed 65mm tall. The tallest part is 110mm.  The longest part is 165mm for the optional RAMBo mount, which can be improved.  The ubiquitous rail segment is 160.6mm long. (The motor mount plate was 177, but it was 2x2 repeat of the part, and I've committed a change to make it a single part.)

If 150x150 is the target build area, the rail_length can be reduced by 15, and the motor_rail_segment length can be increased by 130. I need to double check that that won't cause unfortunate side effects, but it should work.

revarbat, 2015-09-18:
Okay, I've pushed parts size changes so all part are printable in a 150x150mm area.  The only part longer than 150mm is the sled endocarp part.  It's hard to shrink, at 157.7mm, but it can be easily printed diagonally on a square build platform. Not sure how to shrink it below 150 without shrinking the platform width.

ezrec, 2015-09-18:
I'll try printing the 150mm sled end cap, and see if it'll fit on my 180mm delta.

ezrec, 2015-09-18:
Looks like the sled end cap and the yz_joiner_parts both fit! Nicely done.

(Though yz_joiner_parts was very close - I have to turn on off 'brim' and 'skirt', or I get a head crash when it tries to go so close to the edge.

andrewcaustralia, 2015-09-18:
Allowing them to fit in the 150mm bed diagonally is just as good. Do the changes require reprinting existing parts or have they just been modified to suit the current build (I ask as I've already got the STL's downloaded and am printing them out; am about 1/3rd of the way done).

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

ezrec, 2015-09-18:
Additional suggestions:

* Use just a single 'chain_link_part' STL, and let the builder do bed placement for the set.
*  jhead_platform_parts is too big by about 1cm to fit my delta.
* rail_motor_segment_parts is too big by ~1cm
* rail_segment_parts is too big by ~1cm
* sled_parts too big by ~1cm
* .. and the same with spool_holder_parts

All the rest fit (except the RAMBO holder, but I'm using RAMPS, so not my itch to scratch...).

So close!

I'll see if one of my Cartesian friends can print the problematic parts for me.

revarbat, 2015-09-18:
Unfortunately, the length of all rail segments have changed.  You CAN just set rail_length back to 150 and motor_rail_length back to 100 in config.scad, and regenerate your own parts.

I understand your pain, though. I just spent a week printing the parts needed to finally test the direct_drive_z changes, and I found out all the sled pieces have their slop set too tightly, so the sleds have way too much friction.

I'm afraid this is why this printer is still marked experimental.

The sled pieces haven't changed, so you will probably want to keep going with the STLs you have, then download the new sled, and reprint those.  Sadly you will need 8 of them.

If you want to try the last verified working version of the printer, you can go off of the v0.95 branch STLs, though they are for the lifter-rod based Z axis.

revarbat, 2015-09-18:
Ezrec, you can always regenerate the parts after tweaking with the rail_length and motor_rail_length in config.scad.  You can always print half-length rail segments (via rail_length) and use twice as many, for example.

andrewcaustralia, 2015-09-18:
Hey that's no worries mate; just figured I'd check and confirm! I'm sure I'll be reprinting parts for a while making some adjustments myself anyway ;-)

revarbat, 2015-09-18:
Ezrec you may also be able to get good results from reducing platform_width by 10 or so.  That will end up narrowing all the rail parts as well.

ezrec, 2015-09-18:
Thanks! I'll try that.

ArktekniK, 2015-09-19:
>You can always print half-length rail segments (via rail_length) and use twice as many, for example.
This is exactly what I had done - glad to see that you've suggested the same thing. Some quick maths lead me to 69.71 for the rail length. 75mm isn't right as it appears the connectors add about 10 mm to the total. Total of two of them together should be 160.58mm

ArktekniK, 2015-09-19:
>I just spent a week printing the parts needed to finally test the direct_drive_z changes, and I found out all the sled pieces have their slop set too tightly, so the sleds have way too much friction.

Now that you mention it, I was just wondering what the slop calibration part is for? I assume we print it and the values are used in calibrating values for the config.scad?

revarbat, 2015-09-21:
You print a slop calibration part, to figure out the value to plug in to the printer_slop value in config.scad.  The hole that the plug fits into without a lot of effort, has the slop value printed on the side of the block in front of it.

The printer_slop value is used in a lot of places to enlarge or widen fittings where parts fit together.  This includes sliders, joiner tabs, mount holes, etc.

ezrec, 2015-09-21:
Thanks for pointing out the slot calibration part STLs.

Just printed it (55min print time), and got the '10' value as the best fit.

Machine: Geeetech Delta Rostock (modified), Repetier 0.91, E3D v6 Lite (0.8mm nozzle)

Media: PLA (FoxSmart) 1.75mm, 0.7mm layer height, 30% infill, 44mm/s, 210C, no heated bed.

Looks like I should be able to churn these out once I get my new spools.

jkeegan, 2015-09-21:
Brilliant!

On Sun, Sep 20, 2015 at 8:18 PM, Revar Desmera <notifications@github.com>
wrote:

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

--

/=====================================================================\
| Jeff Keegan  ==  jkeegan@keegan.org  ==  http://www.keegan.org/jeff |
\=====================================================================/

revarbat, 2015-09-27:
Okay, just a heads up... I have repeatedly failed to get the direct drive Z axis mods to work, so I'm reverting back to using the two lifter rod design for the Z axis.  This means, for those already having printed a lot of parts, you'll need to print the following new files:
- z_sled_parts.stl
- rail_z_motor_segment_parts.stl
- lifter_rod_coupler_parts.stl
- lifter_lock_nut_parts.stl
- rail_endcap_parts.stl

These replace the follow parts:
- 4 of the 8 sled_parts.stl
- 2 of 4 sled_endcap_parts.stl
- 2 of 4 rail_motor_segment_parts.stl
- Both z_joiner_parts.stl
- 1 of 3 rail_endcap_parts.stl

ArktekniK, 2015-09-28:
Thanks for the info - I just finished printing the XY joiner parts when I saw the new check in for 1.1b. Did a quick comparison and saw it was updated. The two vertical parts with the connectors on top seem to have moved inwards a few millimetres. Will they need to be re-printed too?

revarbat, 2015-09-28:
Yeah, the XY joiners were incorrect due to the earlier parts resizes, so they had to be fixed. You probably need to print one new rail_xy_motor_segment_parts.stl part as well, to get one with side joiners.

3dartsinc, 2016-01-23:
I did not find any download how can i download snappy stl. files

Closed 2015-10-04.

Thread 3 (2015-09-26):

YZ Joiner cable hole problem with crossbeam style walls

ArktekniK, 2015-09-26:
Hi,
I am experiencing lots of shrinkage with the default STLs, so I switch the wall styling and noticed YZ joiner has a problem with crossbeam style walls. The hole is too large and causes the beams not to meet. To be honest, I don't think the hole is needed if you've chosen crossbeam walls.

Lines 98-100 of YZ joiner parts should be wrapped in a conditional
https://github.com/revarbat/snappy-reprap/blob/master/yz_joiner_parts.scad#L98#L100

Something like:
```
// Wiring access hole
if (wall_style != "crossbeams") {
    up(rail_thick+rail_height/4/2) {
      cube([16, joiner_width*3, rail_height/4], center=true);
    }
}
```

ArktekniK, 2015-09-26:
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

revarbat, 2015-09-27:
Good catch.

revarbat, 2015-09-27:
[v1.1 0082da0] Fixed issue #3: YZ Joiner cable hole problem with crossbeam style walls
 1 file changed, 4 insertions(+), 2 deletions(-)

Closed 2015-09-27.

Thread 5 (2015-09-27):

In addition to Issue #3

Salandora, 2015-09-27:
In addition to Issue #3 you also need to wrap the lines
https://github.com/revarbat/snappy-reprap/blob/master/rail_segment_parts.scad#L84-L90

ArktekniK, 2015-09-28:
Was just about to report this too

revarbat, 2015-09-28:
[v1.1 fb36d72] Fixed issue #5: wiring access holes not needed with crossbeam wall styles.
 3 files changed, 23 insertions(+), 8 deletions(-)

Closed 2015-09-28.

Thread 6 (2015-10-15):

YZ Joiner cable hole problem with corrugated style walls

ArktekniK, 2015-10-15:
Hi there, just thought I'd mention that I noticed when this object is sliced without support, the printer will attempt to print unsupported overhangs. This is because the bridge is not a direct line across the gap.

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

revarbat, 2015-10-15:
Oh dear.  I  never really print with the corrugated walls, so I didn't see this.  There will be a number of places with this issue, I think.  It should be fixable by making a frame around the wiring access holes, though.

revarbat, 2015-10-15:
[master 0e05308] Fixed issue #6: Wiring access holes need frames on corrugated walls.
 4 files changed, 42 insertions(+)

Closed 2015-10-15.

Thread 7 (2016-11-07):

Scale model?

jpvlsmv, 2016-11-07:
Would it be possible to virtually build the printer at a size that can be printed out?  It would make a neat desktop toy.

Is the animated graphic rendered from a design file somewhere?

revarbat, 2016-11-26:
Huh.  Should be doable?  The renderings are generated from the full_assembly.scad file.  Should be able to load that file in OpenSCAD, then use F6 to render it with CGAL, which will take half an hour or so, then export it as an STL.  Not sure if it'll confuse the slicer with coincident faces in the joiners, but it'll probably work, I think.

revarbat, 2017-04-03:
The animations and renderings are generated from the full_assembly.scad file.

Closed 2017-04-03.

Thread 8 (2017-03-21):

J-head compatible

farfadet46, 2017-03-21:
Hi, i found your project very intersting but i only this model of Jhead (http://www.threedeeprints.com/product/3d-cam-metal-j-head-v6-hot-end-for-reprap-3d-printer-1-75mm-filament-direct-feed-extruder-0-4mm-nozzle/)
So, can you explain me how to put it in the extruder bridge ?
i have already printed it but it don't stay in.
https://github.com/revarbat/snappy-reprap/blob/master/docs/assembly/extruder_bridge_assembly_4_after.png

regards,

popotropopic3, 2017-03-21:
I used a dremel. I would be happy to chat.

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

farfadet46, 2017-03-22:
A dremel oO, no no no, the j-head are too small to fit and stay in.
i think 'maybe' i need this part ?
https://sc01.alicdn.com/kf/HTB1rm4_GXXXXXb2XVXXq6xXFXXXO/200663255/HTB1rm4_GXXXXXb2XVXXq6xXFXXXO.jpg

Sorry for my english, i'm French, so, some time i don't use the correct grammar :p

popotropopic3, 2017-03-23:
My French is far worse than your English.  haha. Are you using a bowden
setup?

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

farfadet46, 2017-03-23:
hi ! no i think bowden isn't interesting for your printer

i think the thick of the platform is smaller than the J-head

https://sc01.alicdn.com/kf/HTB1rm4_GXXXXXb2XVXXq6xXFXXXO/200663255/HTB1rm4_GXXXXXb2XVXXq6xXFXXXO.jpg
on this picture you can see 4.6 mm my J-head is about 5.9mm

the platform is about 4.5mm.
so maybe you can tell me what i can do to fix the j6head to the platform ?
i see on this https://github.com/revarbat/snappy-reprap/blob/master/docs/assembly/extruder_bridge_assembly_8_after.png maybe the component for fixing the ventilator can fix the j-head in place too ?

I just printed the platform for now ; about 6 hours it's my biggest time of print.
and 2 legs haha :)

best regards

popotropopic3, 2017-03-23:
I just used a few layers of Kapton tape. That helped make it a tight fit.

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

farfadet46, 2017-03-23:
i need 1mm of kapton tape XD ok i print the "extruder_fan_shroud_parts.stl"
wait and see ;)
big thanks !

farfadet46, 2017-03-25:
Hello, i just made an adaptator i'm surprised about how it's easy to make :)
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

if you want to add to your files (i named it 13... i don't know why XD)
[13.zip](https://github.com/revarbat/snappy-reprap/files/870382/13.zip)

revarbat, 2017-03-30:
The E3Dv6 head does not conform to the J-head standard. It conforms to the E3D mount standard.  :) It has different mount dimensions.

I worry that the all-metal E3Dv6 isn't workable anyways. I suspect it will carry too much heat up to its mount point and warp the PLA there. As it is, a J-head with its PEEK barrel gets hot enough to warp the PLA mount point if you don't have the cooling fan running on it. Let me know how your adaptor works for you.

popotropopic3, 2017-03-30:
I figured that out the hard way...

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

Closed 2017-04-03.

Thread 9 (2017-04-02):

ACME threaded rod - metric unitrs

NixonMroq, 2017-04-02:
Could someone please add link or spreadsheet to compatible ACME threaded rod in metric unit?
It is almost impossible to get one of these from BOM list in Europe.

revarbat, 2017-04-03:
I'm actually in the middle of building and testing Snappy v1.5, which does away with the threaded rods completely.

If you still want to work with v1.1, though, you can alter the lifter_rod_pitch value in config.scad from 3.175 to something like 2mm, and regenerate the z_sled_parts.scad and  lifter_lock_nut.scad models.

Just load each scad file into OpenSCAD, render with the F6 key, then export the rendered model to STL from the file menu.

revarbat, 2017-04-03:
You'll probably need to alter the lifter_rod_diam and lifter_rod_length values as well.

Closed 2017-04-03.

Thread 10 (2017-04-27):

Extruder quick-fit?

qwertystop, 2017-04-27:
I just found [this design](http://www.thingiverse.com/thing:19590) for a plate that allows easy swapping of extruders. As-is, though, that design only works for printers that mount the extruder on a bar. Is there any chance of a compatible equivalent for the Snappy? It would be useful to allow the use of e.g. [pellet extruders](https://www.youmagine.com/designs/universal-pellet-extruder-reprap-3d-printing).

revarbat, 2017-04-27:
Hmm. I may need to print one out to work out a compatible geometry.  The Snappy v1.5 changes may make it more challenging as well.

- Revar

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

ManuGithubSteam, 2018-12-18:
The new 3.1 design is quite quick fit, just undo the extruder and unplug it. It depends how you do the cables but my guess is that you can swap it in 3 -5 minutes

revarbat, 2019-02-23:
If someone else wants to implement that specific quick change mount, I can include it, but I've decided not to work on this myself.

Closed 2019-02-23.

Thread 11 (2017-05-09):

Amazon Links lead to unavailable items or confusing items

blade2005, 2017-05-09:
On BOM in the wiki,
1. RAMPS kit is out of stock
2. Power supply, the link doesn't have a 120W or 300W option.
3. Cooling fan is out of stock, https://www.amazon.com/dp/B00E1JO8SG should replace it
4. Speaker wire is unavailable. i couldn't find something suitable 22GA thats as cheap.
5. The heated bed is also unavailable, though I found https://www.amazon.com/dp/B00QQ5Q3BI/ which might be substituted.

revarbat, 2017-05-12:
If this in reference to the v1.1 or the v1.5 Wiki BOM?

blade2005, 2017-05-16:
I just saw this response. Sorry about the delay. I got to this from reprap.org
http://reprap.org/wiki/Snappy which at the bottom led me to this
https://github.com/revarbat/snappy-reprap/wiki/BOM

revarbat, 2017-05-16:
Okay, that's the v1.1 links then.

blade2005, 2017-05-17:
It looks like all the links have been updated. Thanks :D

Closed 2017-05-17.

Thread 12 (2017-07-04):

BOM - drive Gears

BrightSeraph, 2017-07-04:
I am quite conviced you will need 2 drive gears - in v1 they were on the same .stl but v2 has got only 1 on it: https://github.com/revarbat/snappy-reprap/wiki/v2.0-BOM

Love your work!

revarbat, 2017-07-06:
Whoops.  Fixed. Thanks!

Closed 2017-07-06.

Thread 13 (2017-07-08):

BOM for 2.0

bigmt, 2017-07-08:
I am currently printing all of the parts for Snappy 2.0.  I believe the BOM page is missing the bridge segment.  It is in the STL repository, so no issues finding it, but I believe the reference from the BOM is missing.  Great work on the design, I'm having a great time printing everything.  I'm using PETG and am a little concerned with the static friction on the rail segments being a bit high, but will report back if I have any issues.

revarbat, 2017-07-08:
Whoops. Missing bridge segment added to BOM.

You may need to experiment with lubricants for PETG. I use mineral oil for PLA and ABS. Maybe a dry Lubricant like PTFE spray on lube will work.

I suspect the bridge segment may be a couple millimeters too long, by the way. Though I'm unclear if my issues were due to design or warped printing. I had to separate the base of one tower from the X rail by a couple mm to get the Z movement to not stall. I kinda took a break from working on v2 after MakerFaire, so I haven't gotten back to it yet.

Closed 2017-07-08.

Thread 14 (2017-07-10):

Z Axis Issue

franzflasch, 2017-07-10:
Hi!

I just built a snappy 2.0. I think the Z axis needs some redesign. How is this even supposed to work? The z sled parts always get jammed into the z-rail parts, as I think they are just to tight together. Have you ever built and tested the current version of the z-axis design?

I am not sure if it's really a good idea to replace the metal lifter screw rods with printed worm gears.
Any advice to this issue?

revarbat, 2017-07-10:
Does the Z binding go away if you pry the YZ joiner segment a couple mm away from the X axis rail on one side?  I'm starting to think I may have the bridge segments very slightly too long.

franzflasch, 2017-07-10:
Hi revarbat! Thanks for your answer.

I think the problem is that the space between the motor-case of the z-sled part and the z-rail part is just too tight. The bridge segment distance looks OK to me, but I can test that.

But honestly I am thinking of just use the z-axis design from the snappy 1.1 and combine it with the new bridge. I would just print the old z-axis towers and adapt the z-axis-bridge joiner part to the new angle of snappy 2.0.

Do you see any problem in this approach?

franzflasch, 2017-07-12:
Here's a picture, maybe now it's easier for you to see the problem:

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

As you can see I needed to break away some material of the z-rail parts in order to make it work. Otherwise the motor gets stuck.

revarbat, 2017-11-11:
This should be fixed in commit 0370cf7.

Closed 2017-11-11.

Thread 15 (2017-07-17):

I built one! Some issues to clear up

mw0uzo, 2017-07-17:
Hi there. Great work on the design of Snappy II, revarbat! :)

I have built mine in ABS and made several modifications to make it more workable.

1) Filed off plastic on the Z axis that catches on the Z sled. I have not made any modifications to the code, as the issue was found after printing 4 of the parts. Increasing the amount cut out in the design or cutting out a different shape should fix this.

2) Modified config.scad for increased build plate height to accommodate a heated bed. The bed supports printed in ABS work fine at 90 degrees and above. I have been using 100 degrees for several long prints without any sagging or warping of the support plastic, as the corners are significantly cooler than the centre.

config.scad
```
// Standard 200mm square borosilicate glass build platform
glass_width     = 216;   // mm
glass_length    = 214;   // mm
glass_thick     =   4.6;   // mm  3mm glass and 1.6mm bed
```

3) Modified config.scad and cable_chain.scad for a much better chain. The original design and values did not work well for me, they did not hold together strongly, tended to come apart, were stiff and needed some material filed off to work at all. The modifed part and change in dimensions work a zillion times better. The changes propagate to the cable chain mount parts, which will need rerendering and reprinting to fit the modifed sizes.

config.scad
```
// Cable chain dimensions
cable_chain_height = 15;  // mm
cable_chain_width  = 25;  // mm
cable_chain_length = 26;  // 26mm
cable_chain_pivot  =  5;  // 6mm
cable_chain_bump   =  1.5;  // mm
cable_chain_wall   =  3.25;  // mm
```

cable_chain.scad
```
include <config.scad>
use <GDMUtils.scad>

module cable_chain_barrel()
{
	h = cable_chain_height;
	w = cable_chain_width;
	l = cable_chain_length;
	r = cable_chain_pivot/2;

	color("SpringGreen")
	union () {
		difference() {
			up(h/2) cube(size=[w, l-20, h], center=true);
			up(h/2-2/2) chamfcube(size=[w-4*cable_chain_wall, l, h-cable_chain_wall-2], chamfer=2, center=true);
			zrot(40) cube(size=[4, (l-15)/cos(40), 2*cable_chain_wall], center=true);
		}
	}
}
//!cable_chain_barrel();

module cable_chain_mount1()
{
	h = cable_chain_height;
	w = cable_chain_width;
	l = cable_chain_length+2;
	r = cable_chain_pivot/2;

	color("SpringGreen")
	union () {
		difference() {
			// Sides and tabs
			mirror_copy([1,0,0]) {
				translate([(w/2-3*cable_chain_wall/2-printer_slop/2)-0.25, (-l/4)+0.5, h/2]) {
					cube(size=[cable_chain_wall-printer_slop, l/2, h-0], center=true);
				}
			}

            // Swap around these shapes, it works better the other way around!

			// Chamfer Bottom Front
			//translate([0, -l/2, 0]) {
			//	scale([1, tan(30), 1]) xrot(45) cube(size=[w+2, (h/2*sqrt(2))+0, h/2*sqrt(2)], center=true);
			//}

			// Round out top front.
			translate([0, -l/2, h]) {
				difference() {
					cube(size=[w+2, h, h], center=true);
					translate([0, h/2, -h/2]) {
						yrot(90) cylinder(h=w+3, r=(h/2)-0.5, center=true, $fn=32);
					}
				}
			}

			// Pivot Divot
			mirror_copy([1,0,0]) {
				translate([(w-cable_chain_wall)/2, 0, h/2]) {
					translate([(-cable_chain_wall/2-cable_chain_bump/2), (-l/2+r+2.75-printer_slop)+1, 0]) {
						yrot(90) cylinder(h=cable_chain_bump+2, r1=r, r2=r+cable_chain_bump, center=true, $fn=32);
					}
				}
			}
		}
	}
}
//!cable_chain_mount1();

module cable_chain_mount2()
{
	h = cable_chain_height;
	w = cable_chain_width;
	l = cable_chain_length+2;
	r = cable_chain_pivot/2;

	color("SpringGreen")
	union () {
		difference() {
			// Sides and tabs
			mirror_copy([1,0,0]) {
				translate([(w-cable_chain_wall)/2, 0, h/2]) {
					translate([0, l/4, 0])
						cube(size=[cable_chain_wall, l/2, h], center=true);

					translate([0, l/2-h/3, 0])
						yrot(90) cylinder(h=cable_chain_wall, r=cable_chain_pivot/2+1.333, center=true, $fn=64);

					// Pivot bump
					translate([-cable_chain_wall/2-cable_chain_bump/2, (l/2-h/3)+0.5, 0])
						yrot(90) cylinder(h=cable_chain_bump, r1=r, r2=r+cable_chain_bump-0.5, center=true, $fn=32);
				}
			}

			// Chamfer top back
			translate([0, (l/2), h]) {
				for (ang = [5:10:45]) {
					scale([1, sin(ang), cos(ang)]) xrot(45) cube(size=[w+2, h/2*sqrt(2), h/2*sqrt(2)], center=true);
				}
			}
		}
	}
}
//!cable_chain_mount2();

// vim: noexpandtab tabstop=4 shiftwidth=4 softtabstop=4 nowrap
```

4) Snappy II absolutely needs two Z endstop switches on each side. Setting it up is a real pain otherwise. I modified the Z endcap so that the spool holder could be fitted on top, so two switches can be used and two spool holders.

rail_z_endcap_parts.scad
```
include <config.scad>
use <GDMUtils.scad>
use <joiners.scad>

module rail_z_endcap()
{
	joiner_length=40;
	w = z_joiner_spacing + joiner_width;

	color("YellowGreen")
	prerender(convexity=10)
	union() {
		difference() {
			union() {
				// Bottom.
				translate([0, -joiner_length/2, rail_thick/2])
					cube(size=[w, joiner_length, rail_thick], center=true);

				// Back.
				translate([0, -joiner_length+rail_thick/2, rail_height/2]) zrot(90) {
					if (wall_style == "crossbeams")
						sparse_strut(h=rail_height, l=w-0.1, thick=rail_thick, strut=5);
					if (wall_style == "thinwall")
						thinning_wall(h=rail_height, l=w-0.1, thick=rail_thick, strut=5);
					if (wall_style == "corrugated")
						corrugated_wall(h=rail_height, l=w-0.1, thick=rail_thick, strut=5);
                }

				// Endstop clip
				fwd((endstop_depth+2)/2) {
					left((z_joiner_spacing-joiner_width-endstop_thick-2+0.05)/2-5) {
						up(rail_height-(endstop_length+2*2)/2) {
							difference() {
								left(5/2) cube([endstop_thick+2+5, endstop_depth+2, endstop_length+2*2], center=true);
								left(2/2) back(2/2) {
									cube([endstop_thick+2*printer_slop+0.05, endstop_depth+0.05, endstop_length+2*printer_slop], center=true);
									cube([endstop_thick+2*printer_slop-2, endstop_depth+10, endstop_length+2*printer_slop-1], center=true);
								}
							}
							down(endstop_length/2+2+endstop_thick*2/2+5/2-0.05) {
								left((endstop_thick+2)/2+5) {
									right_half() trapezoid([0.05, 0.05], [2*(endstop_thick+2+5), endstop_depth+2], h=endstop_thick*2+5, center=true);
								}
							}
							zspread(endstop_hole_spacing) {
								right(endstop_thick/2-1.5/2+0.05) {
									back(endstop_depth/2+2/2-endstop_hole_inset) {
										scale([0.5, 1, 1]) {
											sphere(d=endstop_screw_size, center=true, $fn=8);
										}
									}
								}
							}
						}
					}
				}
			}

			// Clear space for joiners.
			up(rail_height/2-0.05) {
				joiner_pair_clear(spacing=z_joiner_spacing, h=rail_height, w=joiner_width, a=joiner_angle, clearance=1);
			}
		}

		// Joiner clips.
		up(rail_height/2) {
			xspread(z_joiner_spacing) {

                fwd(0) joiner(h=rail_height, w=joiner_width, l=joiner_length-5/2, a=joiner_angle);
                fwd(rail_height-4) zrot(180) yrot(180) joiner(h=rail_height, w=joiner_width, l=13, a=joiner_angle);

                //fwd(l/2) zrot(180) xspread(z_joiner_spacing) joiner(h=rail_height, w=joiner_width, l=10, a=joiner_angle);
					//back(l/2) xspread(z_joiner_spacing) yrot(180) joiner(h=rail_height, w=joiner_width, l=10, a=joiner_angle);
			}
		}
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
xyzprints, 2017-09-06:
Whoa, that is some intense work out there! Thanks for the .Gcode! (is this .gcode for the marlin firmware?) I'll try to get this z axis to wear up. Also, I thought about using silicon oil for lubricant. would that be a good idea?

mw0uzo, 2017-09-06:
Yeah that would probably work. The problem with thin lubricants is that they soak into the grooves of the plastic and quickly drain away, so you'll go through a bottle or a can fairly quickly and end up with a puddle underneath when you move the machine. Use Vaseline, its cheap and works.

mw0uzo, 2017-09-06:
The gcode will work with Marlin or Repetier. The Z axis will move faster with Marlin. I set a hard limit for the Z axis speed in Repetier. When running the gcode at first with Marlin, watch the axis carefully and be prepared to yank the power if the Z axis gets jammed on one side. It can get wonky and the motors are powerful enough to snap or bend plastic on the bridge.

revarbat, 2017-11-17:
Okay, in order:

1. I've fixed the clearance on the Z rails, and modified the corners of the Z sleds.

2. I've added the thicker build plate value as a comment in config.scad.

3. Cable chains have been updated to use the values and tweaks you gave, more or less.

4. The Z end-caps have been modified so the spool holder can mount on top, and both towers can have a limit switch.  Also, I added a tower-to-tower top brace to help with Z wobble and stalling.

5. The Z rails and sleds used to have rail sliders, but I had great problems with the Z axis stalling and getting stuck.  I was using a single Z motor driver on the RAMPS, though.  I may have to try again with dual drivers.

revarbat, 2017-11-17:
Regarding circles not printing well, that is indeed a problem with backlash. The press-fit drive gears have too much play in them when they change directions.

My solution is to print the drive gears with extra-high infill density, then slide a M3 nut into the slot on the bottom, then thread in a M3 screw (10 or 12mm long) through the nut, then tighten it against the flattened shaft of the drive stepper motor.

It reduces backlash almost completely, at the expense of adding the only two screws to the design.

mw0uzo, 2017-11-20:
Ah great to see the mods make it into the design :)
If you revive the old Z axis design with rails, I can test it. With the current design  I never got two steppers driven off one driver to work reliably, even at maximum current setting. So that might explains the trouble you were having. With separate drivers, i can put a significant amount of force on the Z axis and it will lift slowly without stalling. Any extra friction from rails won't be a problem and with the two Z endstop switches, jamming when misaligned will be less likely?
I'd be happy to test a revised Z axis!
If a new(/old) Z axis is forthcoming, I'll have to dismantle the machine so will try some screws in the gears.

xyzprints, 2017-11-22:
reverbat, can you post the ardunio editable files for marlin firmware? I'm currently trying to make it work with the v6 extruder with the drakon extruder (3:1 gear ratio extruder that is capable of working with multi materials including flexible materials) inside but, I can't make this work if I cant change the settings for the firmware which I am extremly new and bad at.

xyzprints, 2017-11-22:
I'll upload the design it after I make the firmware and confirm that it works

revarbat, 2017-11-23:
RAMPS1.4, with Marlin, with EEPROM support turned on (which I always do), lets you alter the steps per mm live with GCode similar to:

M92 X80 Y80 Z400 E1015 (set steps/mm for each axis)
M500 (store settings to EEPROM)

revarbat, 2017-11-23:
I've updated the RAMPS wiring diagram for the dual driver, dual Z limit switch design.  I'll work on updating the firmware on Friday.

revarbat, 2017-11-23:
Aaaaaand I fixed the image linking issues in the v2.0-Assembly.md wiki page.

revarbat, 2017-11-25:
I have pushed new firmware HEXfiles into the firmware folder, and have added a zip file of the Marlin sources configured for the Snappy without Heated Bed, and with the RepRapDiscount Full Graphic LCD.

revarbat, 2017-11-26:
Added insertion of set screws in for the drive gears.

revarbat, 2018-01-10:
Just checked in branch `v3.0` with the initial design for Snappy3 with substantially improved Z axis.

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

revarbat, 2018-01-10:
I'm marking this resolved as Snappy v3 should fix all the major issues listed.

mw0uzo, 2018-01-17:
Ah wow. Excellent!!!!!

Closed 2018-01-10.

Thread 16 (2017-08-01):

firmware issue?

xyzprints, 2017-08-01:
please note that this is my FIRST yes, FIRST printer (got the parts printed out from a person that I know)
I got a snappy 1.5 and snappy 2.0 downloaded those two. printed some of them ( I was printing the 1.5 and 2.0 version files at the same time mixing everything up does anybody know which parts have changed? I think that the extruder platform got extremely light.) okay, the real deal of this problem is that I installed the hex file firmware on ardunio mega before adding the ramps shield. after that I installed everything except the motors and the end stop switches and the heabed thermistor and power (of course I did installed the motor drivers on the right  place!) I added a full graphics controller module (of course I did installed the firmware that says the full graphics control module and) linked it into a 350w smps and booted it up. one the controller the first screen popped and then it auto-resets by itself. what???? I looked at the .diff file that was attached and tried to copy the firmware on marlin but I couldn't because after some of the lines there was some lines that I cannot find and after that I was back to square one. is there any way to fix this? (btw is it safe to use this heatbed on this printer because it looks like the diff file says that it decreases the heat bed heating speed at a half-but why? and do you need to change the firmware when you make your printer bigger for bigger print volume? is there any stl file that I can get so that I can add a v6 hotend? I don't just cant get why this uses a mk4 nozzle)
Thanks and sorry for the long writing. (just a Korean middle school student working on a project that I am interested in)

xyzprints, 2017-08-01:
update: connecting the usb on my computer makes it work without the power from the smps; only the display is not so bright.

xyzprints, 2017-08-01:
update after having my heated bed attatched +thermistor (do not know the right connection for this) and  I fried my ardunio board part called 'LM1117 5.0 ' does annybody know how to fix this problem? I heard that I could run a exterenal 5v psu am I right? will this work?

Closed 2017-09-01.

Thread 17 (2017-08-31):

#extruder motor down  Firmware update & build volume change is it possible?

xyzprints, 2017-08-31:
I was trying out my snappy and my extruder motor isn't working. is there any possibility of finding the reason? and also, is there anny way of changing the build volume? last can I get the whole .ino file for this firmware? I would like to change some things in that firmware. and also, can I get some tips for the snappy?  like settings for cura.

mw0uzo, 2017-09-06:
Which firmware are you using? Pretty sure I had that problem when setting up Marlin, but now I'm using Repetier as it has backlash compensation - needed to get good circles. There was no backlash I could feel on my Snappy, but it was definitely needed to get good circles.

xyzprints, 2017-09-06:
Thanks for the reply!:)
I'm using the the (official) firmware. also, what is backlash?
I am using a ramps 1.4 and ardunio combo. I have a blow fan always on with 9x9 heat sinks.

mw0uzo, 2017-09-06:
Backlash occurs when the motor changes direction. If it is severe, you can feel it by wobbling the sled from side to side. e.g. if the gear and rack were heavily worn you would feel play in the mechanism. When the build is new, you can't feel anything, but there is a very small amount of backlash. Enough to affect circles!
So use the Repetier firmware I posted in the other thread. Marlin does not have backlash compensation.

mw0uzo, 2017-09-06:
There is a slight issue with the PID settings for the extruder temperature control in the firmware I posted. You might find the extruder temperature drifts up 10 degrees, I'm working on this problem so keep an eye on the temperatures and set it 10 degrees lower using the controller menu when it drifts up too much.

mw0uzo, 2017-09-06:
If you find settings that work well for you, let me know!

xyzprints, 2017-09-06:
Thanks for the reply! looks like that is some kind of wear and tear that I need to note with. I'll check if the firmware works without no problem after I get this z axis working. thanks for the warning! :)

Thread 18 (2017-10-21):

J head compatibility

FUDCO78, 2017-10-21:
Hi, I just want to ask if I can use [this](http://www.geeetech.com/wiki/index.php/PEEK_J-head_short-distance) or [ this](http://www.geeetech.com/wiki/index.php/PEEK_J-head_long-distance) j head instead of that one in BoM.

revarbat, 2017-11-11:
The first one yes, the second one no.  The second one is designed for use with a bowden tube as opposed to a direct drive like the snappy has.

keithellis74, 2018-12-11:
Hi, this looks like a great project.  Will this work printed in PLA?

Closed 2017-11-11.

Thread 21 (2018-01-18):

[Question] Minimim build volume to print all the files ?

Shotman, 2018-01-18:
I didn't see it on the wiki but what's the minimum build volume required to print all the part ? I guess it's self replicating but for instance I have a Monoprice MP Select Mini with a 120*120*120 build volume and I was wondering if it's big enough ?

Thanks

revarbat, 2018-01-18:
I’m afraid the parts, by default, need a 150mm cube build volume for Snappy 3.0.

You *can* change the part lengths in config.scad and regenerate the models for a smaller build volume, but I fear some parts like the extruder platform can’t get much smaller than they already are.

Closed 2018-01-18.

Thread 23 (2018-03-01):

V3.0 extruder link

thannemann, 2018-03-01:
The V3.0 J-head hot end link to the amazon part is out of stock without an estimated replenishment date, is there a recommended replacement? Could this work with a Bowden extruder? I am not sure how the hot end mounts (just looking over the instructions) or will the Bowden be too big to mount

bjbeare, 2018-03-12:
Ditto here.

acorrow, 2018-03-13:
SainStore on eBay. Their listing for the 1.75 mm nozzle j head is slightly different than the model SS-110. I just picked one up and when it gets here I'll see if it fits perfectly and report back. Looks like it will, if anything is off will be the height and not by enough to make a difference I think.

http://r.ebay.com/S5oCA9

acorrow, 2018-03-14:
So heads up, the seller of that item from ebay contacted me to let me know their batch of these is broken and they can't sell them, and they have no more of them in stock, and they are discontinued :)

Sooooo yeah, gotta design a new one :) There's plenty out there that will do the trick, and for cheaper too I think. Just a matter of modding the openscad file. Likely want to update the BOM and stuff at some point, but still.

If i find more of these I'll let you all know.

revarbat, 2018-03-14:
I’ve designed up a new extruder platform for much more common E3Dv6 hot end, and checked into the v3.1 branch. I still need to finish the print cooling fan duct, though.

revarbat, 2018-03-15:
In the mean-time, this JHead extruder should work: http://a.co/eCIpayn

kwaad2, 2018-05-24:
@revarbat Hey, any chance you will be getting around to the part cooling fan for the E3D?
I've got most of my Snappy printed. (Just need the Z screws, and a few assorted random parts, and anything related to Extruder. (getting the E3D V6 3mm Volcano this weekend) Been holding off, as I expect to have to print it a few times to get the fit just right.

Also, any chance you can get the fan to blow from the "back" of the hot end? It's a system I don't think I've ever seen, but makes visibility so much nicer.

Depending on my luck, I will either run RAMPS with a Pi3 Klipper controlling it, or go full on, Duet Wifi.
I plan on having this bad puppy running at ERRF2018. :)

revarbat, 2019-02-23:
I've updated the links in the BOM.

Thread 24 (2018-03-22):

Link for extruder Driver Gear

bjbeare, 2018-03-22:
The link for the extruder drive gear is no longer valid.
Will this one work?
https://www.amazon.com/Witbot-Stainless-Steel-Extruder-Printer/dp/B01KJONSRS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

revarbat, 2018-03-23:
Those should work.

revarbat, 2019-02-23:
I've updated the links in the BOM.

Closed 2019-02-23.

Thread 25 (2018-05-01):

Where/How to install jhead_lock_parts and jhead_barrel_fan_shroud

bjbeare, 2018-05-01:
I've completed the build using v3.1... about to power it up. I don't see how to mount the fans, the jhead_lock_parts or the jhead_barrel_fan_shroud.

revarbat, 2019-02-23:
I'm afraid for the longest time I had the equivalent of writer's block when designing that part.  I finally got past that and I have a workable print cooling fan in my repo, though I'm still finishing the J-Head barrel cooling fan.

bjbeare, 2019-02-25:
I've done a redesign of the xy carriage. I'm pretty happy with the result. I'll post on thingiverse after I test the latest version (sometime this week).

Closed 2019-03-18.

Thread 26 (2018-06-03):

YZ Joiner Parts Non Manifold and cause problems during slicing

klaplume, 2018-06-03:
When I slice the stl file for YZ Joiner Parts, I get empty layers. I guess the mesh is non-manifold, I could fix it up in Blender.

klaplume, 2018-06-09:
The same goes for the jhead platform parts

ManuGithubSteam, 2019-03-08:
Hi

I printed the yz joiners as well and did not have this issue. I used slicerPE to slice it.

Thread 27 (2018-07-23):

BOM error? Rail Z Endcap

karlexceed, 2018-07-23:
Snappy 3 BOM states: "1 | Rail Z Endcap"

But the assembly guide Top Brace Assembly ([https://github.com/revarbat/snappy-reprap/wiki/v3.0-Assembly#top-brace-assembly](here)) Step 2 indicates needing two. Also, the wording is inconsistent (rail Z endcap vs Z rail endstop).

ManuGithubSteam, 2018-12-18:
You need two. There seems to be an error..

revarbat, 2019-02-23:
Thanks!  I've fixed the entry.

Closed 2019-02-23.

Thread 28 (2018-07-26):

include slop calibrator in the instructions

drunkscientist, 2018-07-26:
so after printing basically an entire x or y segment (motor+2 rails, 3 carriage pieces and bed mount parts) i opened the slop calibrator file and found that its not some new(to me) bed leveling thing but in fact for calibrating the files to the printer somehow. maybe there could be some mention of what to do with it for those who arent necessarily familiar with openscad as like, step one of the instructions?

revarbat, 2019-02-23:
I added instructions for the Slop Calibrator to the BOM.

Closed 2019-02-23.

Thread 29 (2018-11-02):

BOM links

Erhannis, 2018-11-02:
Quite a few amazon links in the V3.0 BOM have gone dead; it'd be nice if those got updated.  This may be some people's first printer they build, and they may not be confident they understand how to choose components.  Also, I note that the linked suggested power supply only goes up to 120W, so I'm not sure what to get if I have a heated bed and need 300W.

ManuGithubSteam, 2018-12-18:
Sadly wiki pages do not have pull requests...

Not even sure if the projet is still alive...

Anyway

Here are mine:

Qty	Description	Total Cost	Where Found
1	Power Supply, 120W. (300W w/ Heated Bed)	~$17

1	Controller electronics. (RAMPS1.4+2560+Pololus)	~$30
https://www.amazon.de/dp/B06XSZ9M77/?coliid=I27A2HBLU1ZE55&colid=1JQGPCRENC6K9&psc=0&ref_=lv_ov_lig_dp_it
3	Mechanical microswitch end-stops and wiring.	~$

5	NEMA17 Stepper Motors, 40mm length, 1m cable	~$58
https://www.amazon.de/dp/B07DN97BGL/?coliid=I2MA092WJNIY8B&colid=1JQGPCRENC6K9&psc=0&ref_=lv_ov_lig_dp_it

1	e3dv6lite clone hot end w/heater, thermistor.	~$33
https://www.amazon.de/dp/B018E6THV4/?coliid=I2MXHWAUPOAKNR&colid=1JQGPCRENC6K9&psc=0&ref_=lv_ov_lig_dp_it

2	40mm 12v 0.15A 2-pin cooling fan, 10mm thick.	~$16
https://www.amazon.de/dp/B01CZFUOD0/?coliid=I21VE4U9NBKADG&colid=1JQGPCRENC6K9&psc=0&ref_=lv_ov_lig_dp_it

1m	Wire, dual conductor, 22 gauge, stranded
https://www.amazon.de/dp/B00O7HPL5Q/?coliid=I27HGBPA3QF5KJ&colid=1JQGPCRENC6K9&psc=0&ref_=lv_ov_lig_dp_it

1	Heated Build Platform. (optional)	~$16
Not so sure about this one, did not use one myself.
https://www.amazon.de/Homyl-3D-Drucker-Isolierung-Baumwolle-W%C3%A4rmed%C3%A4mmung-wie-beschrieben/dp/B07K31PJV4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

You'll need the following Hardware to build the cartesian frame:

Qty	Description	Total Cost	Where Found
3.1Kg	Plastic Filament. (@ $13/Kg)	~$41	Amazon.com
1	Extruder Drive Gear	~$ 3
https://www.amazon.de/dp/B06XBZ86Y3/?coliid=I2U35GP298WWX7&colid=1JQGPCRENC6K9&psc=0&ref_=lv_ov_lig_dp_it

1	686 bearing.	~$ 3
https://www.amazon.de/dp/B00K86FC86/?coliid=I39OKM2B719X82&colid=1JQGPCRENC6K9&psc=0&ref_=lv_ov_lig_dp_it

1	Borosilicate glass build platform. (214x200mm)	~$12
https://www.amazon.de/dp/B07BM9MFKJ/?coliid=I3LIP0DSIRR3QB&colid=1JQGPCRENC6K9&psc=0&ref_=lv_ov_lig_dp_it

6	3mm x 12mm socket head screws.	~$ 1	Everywhere.
6	3mm nuts.	~$ 1	Everywhere.

ManuGithubSteam, 2019-01-27:
NOTE:

The motors are the wrong ! version!!!

revarbat, 2019-02-23:
I've updated the links in the BOM.

Closed 2019-02-23.

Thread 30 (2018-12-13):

mk42 bed config

boelle, 2018-12-13:
have anyone made a config for the mk42 bed? it uses the same 4 corner holes but have 2 extra at the center

and then its 250x210 instead

ManuGithubSteam, 2018-12-18:
Im just starting out with my snappy and printing parts but i would suggest its just a mater of changes in the config of the fw how wide the bed is. i belive you dont need the two holes in the middle. There is nothing to attach to anyway.

boelle, 2018-12-18:
the bed is more wide than mk42 but just uses the same corner holes, so there needs to be ~50 more space for the bed

and yes the 2 center holes are needed, the prevent the bed from warping when it gets hot

Closed 2019-03-19.

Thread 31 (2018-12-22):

Can't join lifter rods

brennancheung, 2018-12-22:
I broke 4 lifter rods trying to join them together.  I'm back to 0/4 lifter rods that I can use after a full day of printing.  There is not enough clearance to fit the rod into another rod.  I even tried sanding inside the hole and the fitting beforehand and adding lubricant as well.  I can only insert the piece about half way in before it snaps off.  A tremendous amount of pressure and rocking was needed to even get it that far.  Is there something I'm missing?

coyotebush2384, 2018-12-23:
The design I believe requires them to have a  solid fit I would just try sanding/filing there could be a lot of reasons they dont fit good probly your printer. Use the slope calibration to get parts dialed in. Mine took over 2 weeks and 3-4 printers running basically 24/7 I did build it so I had 2 ft of z height Haha but the point is..it works just have patience

brennancheung, 2018-12-26:
Might something with my settings then.  I still had to use a dead blow hammer to get the pieces in even with changing the dimensions.  I'll close the PR though since it seems like others have had success with the original size.

Closed 2018-12-26.

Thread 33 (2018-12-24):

Firmware help

shade1059, 2018-12-24:
Are there instructions on how to flash the firmware? I am new to marlin. Specifically the LCD screen on the printer says "printer ready" but nothing else, and I do not know where to begin with troubleshooting.

ManuGithubSteam, 2019-01-06:
See here for example: https://www.my-home-fab.de/en/documentations/reprap-firmware/installing-marlin-firmware-on-ramps-1.4
Just leave out step 3 as the firmware is already modifierd for the snappy. So just dont do the modifications.

shade1059, 2019-01-10:
Thank you for the help. The Arduino software tells me that it compiled and flashed correctly, however the LCD screen comes up blank, and my computer fails to connect every time. Through some fiddling with the marlin settings, I can get the LCD screen to say "printer ready 16/0" but it is unresponsive beyond that.

ManuGithubSteam, 2019-01-10:
Hmm things that pop into mind:

- wirering issue
- you fried some part of the mega or ramps ( these boards are so cheap they
have no protection for " upps wire should go here not here)

- what fiddling do you do to get the LCD to work?
- did you try print with octoprint? Maybe LCD just borked

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

ManuGithubSteam, 2019-01-29:
Hi Shade

i have good news.
I was able to compile the stock marlin firmware and get it to work on the ramps 1.4.
I uncommented the lines you mentioned. But i did NOT touch the motherboard line.
I strongly believe, you have to set it to Ramps SOMETHING (can't access config right now...)
Then i flashed it and the lcd did came on and worked with the buttons etc.
However i did not connect the motors and switches etc at that time.

Hardware i use: Mega2560 + Ramps 1.4

Sadly i was not able to compile the snappy marlin Firmware. It gave me an error with the y Endstop.
Did you successful compile the snappy version of the firmware ?

If so, would you upload your sources here ?
Do you know if the snappy firmware does work with the Endstops switched from top to bottom ? (3.1 design)

As said the stock marlin does compile and flash onto the ramps. My Plan for now is to disect the config.h from the marlin and grad usefull stuff while hopefully let it compile and see where i go fro there...

Thanks for the help!

ManuGithubSteam, 2019-01-29:
Ok here it is. My first Marlin Firmware for snappy 3.1.

What did i do:
- basicly comb trough the orginal snappy config and copy all the sensible lines into the new Marlin config.h
- I did enabled a few nice things that are not in original snappy but i tried to keep it simple and not mess up all.
- I did not flip the z axis as it was switched back to the bottom of the z tower in 3.1 design.

It compiles.
So please test it. This is really alpha. I did not even test it on the device. just checked if it compiles!

Basically i think it will work but most likely needs some tinkering.
Please test.

And remember to set your correct motherboard in the config.h
[Marlin_Snappy_Next_v1.tar.gz](https://github.com/revarbat/snappy-reprap/files/2809341/Marlin_Snappy_Next_v1.tar.gz)

ManuGithubSteam, 2019-02-04:
Here is my semi final version.
- Axis go in the correct direction
- Endstops do work.
- Soft Endstops work

Over all this should print quite well. I have some issues with the z rods as they block if they are not 100% flat.
I did not test real printing yet as i have the above issue.

ManuGithubSteam, 2019-02-17:
Ok here is a working version with filament unload etc. I printed a benchy with it

[Marlin_Snappy_Next_v7.zip](https://github.com/revarbat/snappy-reprap/files/2873146/Marlin_Snappy_Next_v7.zip)

ManuGithubSteam, 2019-02-27:
Here is a new verision with curve cuttent to the steppers. Reduces vibrations quite a bit i think:
[Marlin_Snappy_Next_v8.zip](https://github.com/revarbat/snappy-reprap/files/2912245/Marlin_Snappy_Next_v8.zip)

shade1059, 2019-08-04:
Sorry for the delayed response. I was able to get it to work eventually. There were a few issues: The LCD shipped didnt exactly match what I ordered, and I didnt notice. Thus it didnt quite align with the model enabled in the firmware.
Also my power supply was having issues, I ended up getting an new one and all of the motors started working properly. Now I know I have the wrong number of steps per mm on my Z, but just gotta take some simple measurements to fix that (or see what you used in the marlin that you sent me).  I am good with marking this this issue taken care of.

Closed 2019-08-04.

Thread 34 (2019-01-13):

Motor resize doesn't seem right...

NigelThorne, 2019-01-13:
I have a bunch of NEMA 23 style motors that I was give... so I was trying to adjust the plans to with with those.

I replaced all calls to nema_motor_...(17) with nema_motor_...(23), which seems to have increased the space available to account for the bigger motors... however z_base_parts.stl  the legs intersect the motor housing...
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

Is there something else I need to do? Or do I need to make changes in the plans to allow this change?
Cheers
Nigel
BTW... what a great idea for a project... Nice work! Well done for sharing what you have.

dorkmo, 2019-01-13:
Might just throw a difference() in there with nema cube

NigelThorne, 2019-01-14:
:) I fixed this part... I'll raise a pull request... but other parts also need adjusting...

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

I think it will take widening a bunch of pieces... and maybe the motors will be to heavy... I plan to look into it.

revarbat, 2019-02-23:
Looks like you need to increase the `rail_height` in `config.scad` so that the motor fits in the X/Y motor segments.

revarbat, 2019-02-23:
Only two motors should matter for weight, as the Y and extruder motors are the only ones that move.

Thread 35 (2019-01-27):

BUG: rail_z_endcap_parts.stl still has Endstop holders

ManuGithubSteam, 2019-01-27:
Hi

Quite a simple miss i guess:

in the 3.1 Design the Endstops where moved down to the Z Base parts.
However, in the rail_z_endcap_parts.stl there are still present.

These collide with the z lifter rods.

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

I fixed it in TinkerCAD but dont know that much of scad to do it there.

Just to raise awareness :-)

revarbat, 2019-02-23:
Fixed in 6f06297

Closed 2019-02-23.

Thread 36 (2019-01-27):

BUG: Adjustment Screws -> Z sled needs other dimensions as build platform

ManuGithubSteam, 2019-01-27:
Hi

I printed a set of adjustment screws with my sloppy value and they are working fine in the build platform and are nice and tight but still usable.

However i could not risk using these in the z Rail connectors. They where to tight!

To get a good fit there i had to scale them a bit. 98 % shrinkage in x and y direction. Keep the z.

Then they fit into the z parts and work as expected.

revarbat, 2019-02-23:
I've added an explanation of using the Slop Calibrator to the wiki [v3.0-BOM](https://github.com/revarbat/snappy-reprap/wiki/v3.0-BOM) page, before the list of parts to print.

ManuGithubSteam, 2019-02-23:
Hi revbarbat,

Very nice to see you back on the wheel for this!

My sloppy value is 0.07. If there is such a thing as a too tight fit. Please mention it in the Slop Calibrator description :-)

revarbat, 2019-02-24:
In a perfect world, with an ideal 3D printer that printed to exact dimensions, printer_slop would be 0.00.  I've yet to see said perfect printer, though.

revarbat, 2019-02-24:
Though I guess a too-tight fit is one where the plug takes more than light-force to insert and remove in any rotation.

ManuGithubSteam, 2019-02-24:
Hello revarbat,

Well the prusa mk3 has a sloppy value of 0.07 for me. But I need quite a
bit of force to remove the parts once connected. Hence my question if it is
possible to have a too tight fit and have adverse effects like the X
vibration..

Thanks

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

Closed 2019-02-23.

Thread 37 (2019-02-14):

Sliding of Y sled partial assembly on Y axis rail assembly

parth1739, 2019-02-14:
Hi,
Y sled assembly is not sliding smoothly over Y axis rail assembly. I have tried lubricating it with vaseline and mineral oil but t doesn't help. I have also tried filing the parts but didn't help.
Also, I faced problems connecting all the parts. I had file them for hours in order to fix them together and still the results are not good. Has everyone faced similar situations?

coyotebush2384, 2019-02-14:
Yes that's why you would want to use the sloop calibrater and openscad to get parts to print correctly

parth1739, 2019-02-14:
Hey,
Thanks for the prompt reply. I don't know what sloop calibrater is. And I am not familiar with Openscad either. Can you please guide me?

coyotebush2384, 2019-02-14:
I probably can. hopefully someone else will jump in but if not I can give better reply when I get off work

dorkmo, 2019-02-14:
in config.scad look for printer_slop

dorkmo, 2019-02-14:
i saw on forum people talking about this file https://github.com/revarbat/snappy-reprap/blob/master/STLs/slop_calibrator_parts.stl

parth1739, 2019-02-15:
> in config.scad look for printer_slop

Hey Dorkmo,
Thanks for the reply. I opened config.scad and found this -> "printer_slop = 0.20;  // mm". Now I understand that slop callibrater is something which is used to fit parts correctly, but I cannot figure out how do I use it? Also, I have already printed slop callibrator parts.

dorkmo, 2019-02-15:
I havent built a snappy, but i think after you print the slop_calibrator_parts.stl, you trying putting the peg into the holes, after you fiigure out the best fit, you read the number off of the side and define that number in the printer_slop= value. Then that value is used to generate the models for the rest of the snappy. Have you tried placing the peg in the holes? Let us know what it fits in.

dorkmo, 2019-02-15:
On a side note, i couldnt find any reference to the calibrator_parts in the build guide. i think it probably needs a pull request.

parth1739, 2019-02-16:
I did not try it earlier. But now it fits perfectly in "45" and the fit it so strong that the peg is not coming out anymore.

dorkmo, 2019-02-16:
cool. I think that means you should set printer_slop=45; then run the make file

parth1739, 2019-02-17:
Alright. The change in printer_slop value will be done in the configuration file that I have in my system right? The value that is mentioned there right now is ".20". So should I mention the new value as ".45"? How do I run this file?
Also, I have printed almost all the parts and it has taken me a long time. I was hoping there is some way to utilize those parts as well.

dorkmo, 2019-02-17:
I think you might be able to just reprint the parts that are giving you the most trouble? besides the Y axis, how bad off are the other parts? are they wobbly or something else?

After you change the slop value in the config file on your computer, you'll need to use a terminal to run the make command. That executes all the stuff in https://github.com/revarbat/snappy-reprap/blob/master/Makefile which will create custom STL files using the new slop value. At least i think thats my understanding of the readme explination. hope it works out for ya.

parth1739, 2019-02-17:
The parts like sled and motor assembly needs to be smooth in order to slide properly. I think they need a reprint. Also, I was able to fit parts like rail segments and motor assembly after filing but now they are  bouncing back once I join them, bad fit.  Since I got stuck in the initial stage I still got to check the rest of the parts, But I am certain that they would require filing too.
Where will I find the make command? The link  you shared, is that the make command? Also, since I use windows its a bit different for me. I think I have to carry out the modifications for every individual parts. I read something like that in readme file.

dorkmo, 2019-02-17:
Yeah maybe it will be easier to do them individually, just open each file scad file, then press F6 to render it, then go to File > Export > as STL

parth1739, 2019-02-17:
Alright. I will just tell you the process which I followed. Correct me if I went wrong somewhere. Firstly, I changes the slop value in config file. I saved that file. Then I open the design file that I need to make as per the correct dimension and then render it using F6 and then export as stl.
Is that correct or am I missing any step?

dorkmo, 2019-02-17:
yup that should be right. like if you look at https://github.com/revarbat/snappy-reprap/blob/master/xy_sled_parts.scad for example, the first line shows "include <config.scad>", then it uses the slop value from that

parth1739, 2019-02-17:
Great thanks a lot. I am a bit curious about slop calibrater. Was it particularly designed to calibrate the parts as per the user's printer? Is it used in for some other applications also?

dorkmo, 2019-02-17:
i've been doing a lot of guessing, but i think thats its only application.

ManuGithubSteam, 2019-02-17:
After yout put the correct slop value just type make in the main directory and all files will be rerenderd with the corret slop in the STL folder.

parth1739, 2019-02-18:
Thanks @ManuGithubSteam . Can you tell me what do you mean by main directory and where can I find it?
@dorkmo  I came across another problem today. I tried putting the peg of slop calibrater in other holes and found that it is fit for other holes also. Like its going easily in 45, 40, 35 etc.. What do I do in this situation?

parth1739, 2019-02-20:
Hi,
When I was rendering the Y_z joiner parts I received a warning stating "Object may not be a valid 2-manifold and may need repair!"

ManuGithubSteam, 2019-02-20:
Hi

The main directory is the directory, that you download from githup or the
one that gets created when you clone the repo. It has a subfolder STL and a
file called Make in it.

Slic3r might be able to repair your broken STL file.

Hope that helps

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

revarbat, 2019-02-22:
Yes, that should be 0.45, not 45.
Also, 0.45 is a very large printer_slop value.  Are you sure your current printer is printing square and isn't wobbling on the Z axis over much?

- Revar

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

revarbat, 2019-02-23:
I've added an explanation of using the Slop Calibrator to the wiki [v3.0-BOM](https://github.com/revarbat/snappy-reprap/wiki/v3.0-BOM) page, before the list of parts to print.

parth1739, 2019-02-23:
> Yes, that should be 0.45, not 45. Also, 0.45 is a very large printer_slop value. Are you sure your current printer is printing square and isn't wobbling on the Z axis over much? - Revar
> […](#)
> On Feb 16, 2019, at 9:31 PM, parth1739 ***@***.***> wrote: Alright. The change in printer_slop value will be done in the configuration file that I have in my system right? The value that is mentioned there right now is ".20". So should I mention the new value as ".45"? How do I run this file? Also, I have printed almost all the parts and it has taken me a long time. I was hoping there is some way to utilize those parts as well. — You are receiving this because you are subscribed to this thread. Reply to this email directly, view it on GitHub <[#37 (comment)](https://github.com/revarbat/snappy-reprap/issues/37#issuecomment-464419333)>, or mute the thread <https://github.com/notifications/unsubscribe-auth/AAVXMedgn3jG68NsJB7epC14n7fm1h-Yks5vOOlAgaJpZM4a7yUj>.

Hey @revarbat
Earlier the peg was not a good fit with any hole except 0.45. But now I guess with smoothing due to push in and pull out it is fitting in other holes aswell.  I currently have 2 printers. As per your new instructions on github page I think now slop value for one of my printer in .40 and the other is .35.
Talking about wobbling  of z-axis of current printer. It does vibrates a bit while printing but I haven't confirmed whether its printing exact square or not. Any added instructions from your end could be useful for me.

Thanks

parth1739, 2019-02-23:
> Hi The main directory is the directory, that you download from githup or the one that gets created when you clone the repo. It has a subfolder STL and a file called Make in it. Slic3r might be able to repair your broken STL file. Hope that helps
> […](#)
> On Wed, 20 Feb 2019, 04:09 parth1739 ***@***.*** wrote: Hi, When I was rendering the Y_z joiner parts I received a warning stating "Object may not be a valid 2-manifold and may need repair!" — You are receiving this because you were mentioned. Reply to this email directly, view it on GitHub <[#37 (comment)](https://github.com/revarbat/snappy-reprap/issues/37#issuecomment-465403235)>, or mute the thread <https://github.com/notifications/unsubscribe-auth/ADS_4gMFg4YLjpa3WuEQr9lXc_4ejBh4ks5vPLxogaJpZM4a7yUj> .

Hi @ManuGithubSteam
Alright now I understand what the main directory is. I also found the makefile in it. Could tell me where in the main directory should I  type "make" to render files in STL folder.

Closed 2019-02-23.

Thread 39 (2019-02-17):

X axis movement -> very high vibrations ruin print, Y Axis ok

ManuGithubSteam, 2019-02-17:
Hi Guys,

I just finished my snappy 3.1 and its an amazing machine. However, i have some bad vibrations when the x axis is moving. So bad in fact, that it ruins the print. Moves in y axis are fine and they look really good. But all the moves in the x direction do vibrate so much, that there are artifacts in the print and that constantly. It just vibrates too much.

Any ideas why the x axis is vibrating that much ? Could this be that there is not enough current on the x stepper motor?

Thanks

dorkmo, 2019-02-18:
you might upload a video to youtube

ManuGithubSteam, 2019-02-18:
There you go: https://youtu.be/dKV7vusrJ4g
Hope it helps
Any ideas ?
Thanks!

revarbat, 2019-02-23:
Try lubricating the sliders and/or the gear racks with vasoline.  Don't know if that'll help or not.  I'm seeing some excess vibration on my own X axis, and I'm worried that it may be because the drive motor is working against more of a lever arm at the ends of the sled racks.

ManuGithubSteam, 2019-02-23:
Hi revarbat,

Nice to see you back! I'm building this snappy for a school cooperation and it would be super if we could get to the bottom of this :-)

I tired so far:

- Increase current on the x axis motor = no effect
- reduce jerk settings to 2 = could have helped a bit not sure
- decrease x motor acceleration to 200 = This helped

The problem with the decrease of the acceleration i fear is: The problem gets better to to totally avoid it i would have to decrease the acceleration probably to 50 or even less.

Is there a minimum amount of acceleration ? What does this mean print time wise ?

Also when i reduces the jerk settings, the print time got way longer.

I saw a firmware setting, to immediately accelerate to motors could that help ?

Speaking of firmware: I tried to model my version after your settings, but i'm not sure if i have the best configuration. If you want you can use my version as a base for 3.1 firmware :-)

Here are some photos from a benchy with 200 x accel:

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

revarbat, 2019-02-24:
When I slowed my acceleration, it mostly just made the wavelength of the ripples longer.  While my prints show the ripples at the ends of longer X motions, your images seem to show ripples at the middle of the print.  I don't feel vibration as I manually slide my X axis by hand, but I can see it when printing.  Perhaps it's because the drive gear pushes the rack (and thereby sled) towards just one side?

ManuGithubSteam, 2019-02-24:
Hi

Yes i have a similar experience. When i use marlin to move the axis it is very smooth without vibration i believe. But when i print gcode there is vibration. When i print, it seems that the vibration only occurs in the direction to the right but not on the back move. However the benchy has the ripples on both sides. So it is present also on the back move.

I now use x acceleration of 100 and the ripples are much less but still there. What acceleration do you use ? Could this issue arise because of incorrect stepps at the motor ?

ManuGithubSteam, 2019-02-24:
Ok 80 mm/sec x accel and lithium grease on the rails seem to have nearly fixed the issue for me. I think i will go down to 70 mm/sec to make them even less visible but the downside is, that the print time nearly doubles. But i'm glad i can produce decent prints.

I will report back in detail with a picture, when the print has finished...

Here is my config.

[Slic3r_config_bundle.ini.txt](https://github.com/revarbat/snappy-reprap/files/2898237/Slic3r_config_bundle.ini.txt)

ManuGithubSteam, 2019-02-28:
Ok so now im printing with 65 mm/sec x axis acceleration and the vibrations are still there but only visible if you look directly for them. So the issue remains but this is a workaround i would suggest.
Also i enabled curved acceleration in the firmware but that does not help so much only on small parts it makes a difference...

ManuGithubSteam, 2019-03-24:
Hi @revarbat
Ok i have more info on this issue:

1. I mitigated the vibrations as i wrote above by reducing the a axis acceleration down to 60mm/s (from 400) i also set the feedrate to 150 mm/sec. I did this in the speed settings of the "print" profile (Accerlation for perimeters 60) and as a setting in the Printer profile (Machine Limits). In the Firmware i left it on 400.

This helped to make the vibrations barely visible. But they are still there.

 2. After that i switched from A9688 to TMC2208 in an effort to make the printer more silent. I switched out X, Y and Z stepper drivers. This worked like a charm and the printer is now super silent.

However as the TMC2208 does advertise speed gain while maintaining print quality i tried some faster speeds. In the end i can say that even with 400mm/s acceleration the loss in quality is like 10% to the quality when printing with 65mm/sec speed.

So the drivers helped to get rid of the excess print time. For me this is a huge win. However it got me thinking. If the TMC can print with less vibrations, doesn't this mean that the vibration is caused by "uneven" sinus signal curve of voltage, as the TMC does essentially smooth out the uneven current into a smooth more sinus curve like curve.

If this is the case could we get rid of the vibrations nearly all together if we dial in the voltage exactly on the amount that is needed and just enough to no skip steps ?

Sadly i could not try this out as i had to deliver my snappy to the school and i had to eyeball the amount fast.

Other ideas i had to maybe solve this:

- Make the y axis heavier and so not so much vibrations transfer might occur ?
- Make a second line of fish grip rails for the gears so the gear is gripped from two sides not just one
- Make a padding of some sort for the x motor, That not so much vibration is transfered to the rails via direct contact with the motor. For other cartesian printers there a special dampeners for this.
--> It could be enough to not let the motor contact on the top of the rails and only have a hold further down and on the 4 corners ?

I hope we find a solution before they finish printing their snappy on mine :-)

PhilMegman, 2020-05-12:
Hi everyone,

did you concider the "stick-slip phenomenon" as reason for your issue? https://en.wikipedia.org/wiki/Stick-slip_phenomenon

My snappy has a different issue, but I think it is caused by the stick-slip phenomenon. (It is not performing small movements in X-axis.)

So if anyone knows a solution for this I would like to hear it.

Best regards

revarbat, 2020-05-12:
I'm not exactly an engineer.  My best guess is that we need a better lubricant than mineral oil or vaseline. My experience with various lubricants is as follows:
- Vegetable oil worked, but will eventually go rancid.
- Mineral oil works, but I still get vibration in my builds. I also have to re-apply it periodically.
- Vaseline doesn't need to be re-applied as often, but it has more friction, and I still get vibration in my builds.
- 3-in-1 oil slowly soaks into the PLA of the rails, expands them, and makes them bind.
- Spray-on dry PTFE lube actually made the rails have *more* friction.

I gather that many petroleum based lubricants may degrade plastics over time anyways.

Some things to try:
- Graphite dry lubricant
- ???

ManuGithubSteam, 2020-05-12:
Hi guys,

Just to chip in; I tried graphite based lubricant on the X axis and it
helped but not so much that I could actually print with the snappy. For now
this project is dormant for me.

However if the version gets fixed I will gladly resume it.

I also have some designed parts that where missing or did not fit with my
motor's. If interested I can share them with you.

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

revarbat, 2020-05-12:
I'se seen recommendations for white lithium grease and silicone based lubricants for use with PLA and ABS.

revarbat, 2020-05-12:
Regarding having herringbone racks on both sides of the drive gears, that has the problem that the two sides of gear are moving in opposite directions.

I have been thinking, though, about making a screw drive for X and Y similar to the Z axis lifter rods.  That wouldn't have the issues that the herringbone rack has on applying pressure to only one side.  May have more issues with backlash, though.  Also may limit the speed of the X and Y axes.

dorkmo, 2020-05-13:
ive used this in other projects, its okay but still not a magic bullet.
https://www.super-lube.com/silicone-lubricating-grease-with-syncolon-ptfe

PhilMegman, 2020-05-13:
> I'm not exactly an engineer. My best guess is that we need a better lubricant than mineral oil or vaseline.  [...]
>

I've tested different lubricants too and all of them change the behavior while the sled moves, but none of them changed the behavior from start up.

Simple test: Take only the three rail parts and the sled. Both clean of grease. Make them a "Inclined plane" and see the angle when the sled starts moving. Repeat the test with grease. Don't shake it ot touch the sled. In my tests the angle was always nearly the same. With some grease it get's worst. But none of the grease caused a smaller angle (less static friction).

I've glued the three parts of each rail together to get more stiffness. In addition I've re-printed the Y-sled with smaller slop. After this, I had no vibration any more. I still have ghosting, but no vibrations visible on the perimeters.

BUT now I have a different problem, that was maybe hided by the vibrations before:
As mentioned in my post before, my snappy does not make small movements in X-direction. And for longer moves it just stops before a corner instead of moving slow. That leads to a calibration cube (20mm x20mm x20mm) with X:19.3mm Y:20.4mm Z:20.4mm.

Grease as mentione before doesn't helped
Higher current on the steppers does not lead to a solution, but melts the drive gear, finally.

Maybe we need to think about smaller touching area of the sled to the rail...
I think I will try a different material for sled or rail next. Maybe PLA on PLA have a too high static friction. Maybe I try one part in PETG or I try to get metal in between the two PLA parts.

M15631563b, 2024-07-04:
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

If you don't have a hot container, try soap

M15631563b, 2024-07-04:
If the hot container hardens, it will not damage the soap.  Try vegetable soap or margarine

>

M15631563b, 2024-07-04:
I doubt that lubrication can solve your problem.  Check the bearing of the stepper motor, especially the spring at the bottom of the shaft

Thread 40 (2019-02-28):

Filament is escaping the extruder idler

ManuGithubSteam, 2019-02-28:
As you can see the filament is escaping the idler to the side. This leads to the phenomena that there is no more extrusion taking place and the print is ruined.

I made a fix for it here but wanted to raise the issue to fix it at the source. (I cant do openscad so i fixed it in tinkercad): https://www.thingiverse.com/thing:3459378
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

revarbat, 2019-03-23:
Ah. Your drive gear doesn't have the self-centering groove that the mk8 drive gear has.
https://folgertech.com/products/mk8-drive-gear-for-reprap-extruder-5mm-bore-and-7mm-effective-dia-mk-8

ManuGithubSteam, 2019-03-23:
Hi Revar,

I was under the impression, that the groves in that gear would off center
the filament path into the extruder. And did not use it. Is this the case?
I just did a visual check...

Have a nice day
Manuel

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

revarbat, 2019-03-23:
You can just re-center the drive gear groove over your filament path by re-adjusting where it is on the motor shaft.  Up to and including turning it around backwards.  Shouldn't need to, though.  In any case, as you've found out the hard way, the groove keeps it in line.

- Revar

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

ManuGithubSteam, 2019-03-24:
Hello Revar,

I know but I mean not in the X direction where I can slide the gear into
position. I mean in the y direction. So to speak that the groved gear
"hole" (seen from top) is not centerd on the hole below because of the
groved out material. As I see it with the grove it is not a straight line
anymore. But I could be wrong.

Also: in the assembly manual the gear looks more like mine and not a groved
one.
Manu

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

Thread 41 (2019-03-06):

Use TMC2208 with snappy?

ManuGithubSteam, 2019-03-06:
Hi

Can i use the TMC2208 with the snappy ? What does change step wise?

In "normal" printers if you go from A96888 to TMC you have to double or half you steps für x and y.

Is this the case here too?

Thanks
Manuel

ManuGithubSteam, 2019-03-10:
Ok i tried it out.
Its just a drop in replacement, no need to change the stepper drivers. Just plug the tmc in and reverse the direction if x,y and z.

Attention, I did not use the tmc at the e axis as this can cause issues as far as the internet is concernd.

Here is a firmware zip with it.

Have fun
[Marlin_Snappy_Next_v8_tmc2208.zip](https://github.com/revarbat/snappy-reprap/files/2949579/Marlin_Snappy_Next_v8_tmc2208.zip)

Closed 2019-03-10.

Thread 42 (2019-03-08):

Request: Make the holes for the cables bigger in the rail parts

ManuGithubSteam, 2019-03-08:
Hi

Im having trouble putting all the cables trough the holes. Some Cables are thicker etc. Could you make the holes bigger ? I would guess: 0,25 mm left and right and top would be sufficent.

Thanks

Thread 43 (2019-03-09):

Can not get makefile to exicute

mlpage34, 2019-03-09:
I have installed lmde3 and installed openscad, after changing the makefile, I try to run make, and get a syntax error on the first line <!DOCTYPE html>.
I have tried my google fu and it is not strong. can someone point me in a direction to go in order to find a solution?

revarbat, 2019-03-09:
What error does it give?

mlpage34, 2019-03-09:
Makefile:7: *** missing separator.  Stop.

ManuGithubSteam, 2019-03-10:
What system do you use ? Linux or Windows or Mac ? The text editor you use must be capable of using the right end of line (Unix) and you need to save it in unix format.

mlpage34, 2019-03-10:
that was using linux. I can install a different distribution, thats not a problem. I have ubuntu, xubuntu, lmde, kali, debian 9, kubuntu, and lubuntu. also, I can use a diffrent editor. I used nano to modify it last time. It was my intention to use LMDE 3 only for 3d printing, but if I would have better support with fedora, debian, or ubuntu, I would swich

ManuGithubSteam, 2019-03-10:
No thats all fine. So its a logical error in the file, Made by you and no machine can exacly say what it is but its on line 7.
best idea: See the orginal file and compare line 7. It seems some seperator is missing. It seems like you should not modiy that line (7). I did not when i made mine.

I attached mine. It works.

[Makefile.txt](https://github.com/revarbat/snappy-reprap/files/2949713/Makefile.txt)

ManuGithubSteam, 2019-03-20:
could you solve it ?

mlpage34, 2019-03-21:
Yes, it was because I didnt clone the repository. the makefile was full of html and xml language. once I cloned, everything was good

Closed 2019-03-21.

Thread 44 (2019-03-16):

Request: less vitamins,(with solution)

ManuGithubSteam, 2019-03-16:
Hi

I'm looking into ways to get less vitamins for the snappy.

What you can do:

- for the y gears part: Use gyroid infill 75 % and make it tight! and use expo glue to glue the shaft in.
This works if you file the rails down with 400,600,800 and 100 grit sandpaper.
Then we safe 1 screw and one nut :-)

WARNING: You NEED a screw for the x axis gears.!!! I tried it! The x axis is much heavier and needs to be secured with a screw.

To test:

- Screws on the z axis.

revarbat, 2019-03-23:
Iiinteresting.  I originally tried press fit, but I ended up with the shaft loosening, even keyed.  So I put in the screws.  I'd already had a place to put the screws, luckily.  I didn't really get around to trying high-density or alternate infills.  The new slic3r gyroid infills look really interesting.

ManuGithubSteam, 2019-03-23:
Hi ;)

Yes but it only worked on the y rail for me. The X is just to heavy.

But I can imagine that petg with gyroid could hold as it has more give and
is not so brittle. This would need testing but my snappy is in production
already.

Thanks

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

ManuGithubSteam, 2019-08-10:
Ok did some more tests. It does not work. You need the screw in the y and x asis.

Closed 2019-08-10.

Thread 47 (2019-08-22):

Cura Settings

Pteppic1, 2019-08-22:
Hello,
I've just finished assembling and building my first snappy3. I felt a bit like Dr Frankenstein when it first started moving ^^
Now that it works i (naturally) want to use it. Since i'm fairly new to 3DPrinting i have thus far relied on preconfigured slicers (PrusaControl). Since snappy does not have such software i'm a bit lost.
How do i set up Cura or Slic3r to work with this device? Can i just run it "out of the box" with the "generic reprap" settings?
Any help or tips are much appreciated

Thanks in advance

revarbat, 2019-08-23:
As I remember it, you can use generic reprap settings, with the following specifics:
- Build volume is about 195 x 195 x 200mm.
- Print speed should be about 40mm/sec or less.
- Travel speed should be 60mm/sec or less.
- G-Code target type is Marlin.

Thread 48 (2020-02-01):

Z Axis Lifer Rods Not Lining Up

bthayer3, 2020-02-01:
When I printed the rods out and tried to stack them, I noticed the connection point is not exactly flush or smooth at the connection point where the rods are stacked. I am currently having issues with finishing my printer because my sled gets caught at this section prohibiting me from printing tall prints.

I moved the rod into modeling software and stacked a copy of itself on top and noticed there is an overhang as shown in the images below. Is this an issue with the model? I know we have to re-generate the files using Open Scad, could this possibly be an issue that resulted from that?

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

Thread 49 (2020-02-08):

Make errors.

anastazya, 2020-02-08:
./stl_normalize.py -c STLs/bridge_segment_parts.stl -o STLs/bridge_segment_parts.stl
/Applications/OpenSCAD.app/Contents/MacOS/OpenSCAD -m make -o STLs/cable_chain_link_parts.stl cable_chain_link_parts.scad
WARNING: rx was assigned on line 402 of "GDMUtils.scad" but was overwritten on line 404
WARNING: ry was assigned on line 403 of "GDMUtils.scad" but was overwritten on line 405
WARNING: variable center not specified as parameter, in file cable_chain.scad, line 16
WARNING: Too many unnamed arguments supplied, in file GDMUtils.scad, line 857
WARNING: Too many unnamed arguments supplied, in file GDMUtils.scad, line 857
WARNING: Too many unnamed arguments supplied, in file GDMUtils.scad, line 857
WARNING: Too many unnamed arguments supplied, in file GDMUtils.scad, line 857
WARNING: variable center not specified as parameter, in file cable_chain.scad, line 16
WARNING: Too many unnamed arguments supplied, in file GDMUtils.scad, line 857
WARNING: Too many unnamed arguments supplied, in file GDMUtils.scad, line 857
WARNING: Too many unnamed arguments supplied, in file GDMUtils.scad, line 857
WARNING: Too many unnamed arguments supplied, in file GDMUtils.scad, line 857
WARNING: variable center not specified as parameter, in file cable_chain.scad, line 16
WARNING: Too many unnamed arguments supplied, in file GDMUtils.scad, line 857
WARNING: Too many unnamed arguments supplied, in file GDMUtils.scad, line 857
WARNING: Too many unnamed arguments supplied, in file GDMUtils.scad, line 857
WARNING: Too many unnamed arguments supplied, in file GDMUtils.scad, line 857
WARNING: variable center not specified as parameter, in file cable_chain.scad, line 16
WARNING: Too many unnamed arguments supplied, in file GDMUtils.scad, line 857
WARNING: Too many unnamed arguments supplied, in file GDMUtils.scad, line 857
WARNING: Too many unnamed arguments supplied, in file GDMUtils.scad, line 857
WARNING: Too many unnamed arguments supplied, in file GDMUtils.scad, line 857
WARNING: variable center not specified as parameter, in file cable_chain.scad, line 16
WARNING: Too many unnamed arguments supplied, in file GDMUtils.scad, line 857
WARNING: Too many unnamed arguments supplied, in file GDMUtils.scad, line 857
WARNING: Too many unnamed arguments supplied, in file GDMUtils.scad, line 857
WARNING: Too many unnamed arguments supplied, in file GDMUtils.scad, line 857
WARNING: variable center not specified as parameter, in file cable_chain.scad, line 16
WARNING: Too many unnamed arguments supplied, in file GDMUtils.scad, line 857
WARNING: Too many unnamed arguments supplied, in file GDMUtils.scad, line 857
WARNING: Too many unnamed arguments supplied, in file GDMUtils.scad, line 857
WARNING: Too many unnamed arguments supplied, in file GDMUtils.scad, line 857
WARNING: variable center not specified as parameter, in file cable_chain.scad, line 16
WARNING: Too many unnamed arguments supplied, in file GDMUtils.scad, line 857
WARNING: Too many unnamed arguments supplied, in file GDMUtils.scad, line 857
WARNING: Too many unnamed arguments supplied, in file GDMUtils.scad, line 857
WARNING: Too many unnamed arguments supplied, in file GDMUtils.scad, line 857
WARNING: variable center not specified as parameter, in file cable_chain.scad, line 16
WARNING: Too many unnamed arguments supplied, in file GDMUtils.scad, line 857
WARNING: Too many unnamed arguments supplied, in file GDMUtils.scad, line 857
WARNING: Too many unnamed arguments supplied, in file GDMUtils.scad, line 857
WARNING: Too many unnamed arguments supplied, in file GDMUtils.scad, line 857
WARNING: variable center not specified as parameter, in file cable_chain.scad, line 16
WARNING: Too many unnamed arguments supplied, in file GDMUtils.scad, line 857
WARNING: Too many unnamed arguments supplied, in file GDMUtils.scad, line 857
WARNING: Too many unnamed arguments supplied, in file GDMUtils.scad, line 857
WARNING: Too many unnamed arguments supplied, in file GDMUtils.scad, line 857
WARNING: variable center not specified as parameter, in file cable_chain.scad, line 16
WARNING: Too many unnamed arguments supplied, in file GDMUtils.scad, line 857
WARNING: Too many unnamed arguments supplied, in file GDMUtils.scad, line 857
WARNING: Too many unnamed arguments supplied, in file GDMUtils.scad, line 857
WARNING: Too many unnamed arguments supplied, in file GDMUtils.scad, line 857
WARNING: variable center not specified as parameter, in file cable_chain.scad, line 16
WARNING: Too many unnamed arguments supplied, in file GDMUtils.scad, line 857
WARNING: Too many unnamed arguments supplied, in file GDMUtils.scad, line 857
WARNING: Too many unnamed arguments supplied, in file GDMUtils.scad, line 857
WARNING: Too many unnamed arguments supplied, in file GDMUtils.scad, line 857
WARNING: variable center not specified as parameter, in file cable_chain.scad, line 16
WARNING: Too many unnamed arguments supplied, in file GDMUtils.scad, line 857
WARNING: Too many unnamed arguments supplied, in file GDMUtils.scad, line 857
WARNING: Too many unnamed arguments supplied, in file GDMUtils.scad, line 857
WARNING: Too many unnamed arguments supplied, in file GDMUtils.scad, line 857
WARNING: variable center not specified as parameter, in file cable_chain.scad, line 16
WARNING: Too many unnamed arguments supplied, in file GDMUtils.scad, line 857
WARNING: Too many unnamed arguments supplied, in file GDMUtils.scad, line 857
WARNING: Too many unnamed arguments supplied, in file GDMUtils.scad, line 857
WARNING: Too many unnamed arguments supplied, in file GDMUtils.scad, line 857
WARNING: variable center not specified as parameter, in file cable_chain.scad, line 16
WARNING: Too many unnamed arguments supplied, in file GDMUtils.scad, line 857
WARNING: Too many unnamed arguments supplied, in file GDMUtils.scad, line 857
WARNING: Too many unnamed arguments supplied, in file GDMUtils.scad, line 857
WARNING: Too many unnamed arguments supplied, in file GDMUtils.scad, line 857
WARNING: variable center not specified as parameter, in file cable_chain.scad, line 16
WARNING: Too many unnamed arguments supplied, in file GDMUtils.scad, line 857
WARNING: Too many unnamed arguments supplied, in file GDMUtils.scad, line 857
WARNING: Too many unnamed arguments supplied, in file GDMUtils.scad, line 857
WARNING: Too many unnamed arguments supplied, in file GDMUtils.scad, line 857
WARNING: variable center not specified as parameter, in file cable_chain.scad, line 16
WARNING: Too many unnamed arguments supplied, in file GDMUtils.scad, line 857
WARNING: Too many unnamed arguments supplied, in file GDMUtils.scad, line 857
WARNING: Too many unnamed arguments supplied, in file GDMUtils.scad, line 857
WARNING: Too many unnamed arguments supplied, in file GDMUtils.scad, line 857
./stl_normalize.py -c STLs/cable_chain_link_parts.stl -o STLs/cable_chain_link_parts.stl
/Applications/OpenSCAD.app/Contents/MacOS/OpenSCAD -m make -o STLs/cable_chain_mount_parts.stl cable_chain_mount_parts.scad
WARNING: rx was assigned on line 402 of "GDMUtils.scad" but was overwritten on line 404
WARNING: ry was assigned on line 403 of "GDMUtils.scad" but was overwritten on line 405
WARNING: Ignoring unknown variable '$do_prerender', in file GDMUtils.scad, line 7.
WARNING: variable center not specified as parameter, in file cable_chain.scad, line 16
WARNING: Too many unnamed arguments supplied, in file GDMUtils.scad, line 857
WARNING: Too many unnamed arguments supplied, in file GDMUtils.scad, line 857
WARNING: Too many unnamed arguments supplied, in file GDMUtils.scad, line 857
WARNING: Too many unnamed arguments supplied, in file GDMUtils.scad, line 857
WARNING: Ignoring unknown variable '$do_prerender', in file GDMUtils.scad, line 7.
WARNING: variable center not specified as parameter, in file cable_chain.scad, line 16
WARNING: Too many unnamed arguments supplied, in file GDMUtils.scad, line 857
WARNING: Too many unnamed arguments supplied, in file GDMUtils.scad, line 857
WARNING: Too many unnamed arguments supplied, in file GDMUtils.scad, line 857
WARNING: Too many unnamed arguments supplied, in file GDMUtils.scad, line 857
WARNING: Ignoring unknown variable '$do_prerender', in file GDMUtils.scad, line 7.
WARNING: variable center not specified as parameter, in file cable_chain.scad, line 16
WARNING: Too many unnamed arguments supplied, in file GDMUtils.scad, line 857
WARNING: Too many unnamed arguments supplied, in file GDMUtils.scad, line 857
WARNING: Too many unnamed arguments supplied, in file GDMUtils.scad, line 857
WARNING: Too many unnamed arguments supplied, in file GDMUtils.scad, line 857
WARNING: Ignoring unknown variable '$do_prerender', in file GDMUtils.scad, line 7.
WARNING: variable center not specified as parameter, in file cable_chain.scad, line 16
WARNING: Too many unnamed arguments supplied, in file GDMUtils.scad, line 857
WARNING: Too many unnamed arguments supplied, in file GDMUtils.scad, line 857
WARNING: Too many unnamed arguments supplied, in file GDMUtils.scad, line 857
WARNING: Too many unnamed arguments supplied, in file GDMUtils.scad, line 857
WARNING: variable center not specified as parameter, in file cable_chain.scad, line 16
WARNING: Too many unnamed arguments supplied, in file GDMUtils.scad, line 857
WARNING: Too many unnamed arguments supplied, in file GDMUtils.scad, line 857
WARNING: Too many unnamed arguments supplied, in file GDMUtils.scad, line 857
WARNING: Too many unnamed arguments supplied, in file GDMUtils.scad, line 857
WARNING: variable l not specified as parameter, in file cable_chain_mount_parts.scad, line 94
WARNING: Ignoring unknown variable '$do_prerender', in file GDMUtils.scad, line 7.
WARNING: variable center not specified as parameter, in file cable_chain.scad, line 16
WARNING: Too many unnamed arguments supplied, in file GDMUtils.scad, line 857
WARNING: Too many unnamed arguments supplied, in file GDMUtils.scad, line 857
WARNING: Too many unnamed arguments supplied, in file GDMUtils.scad, line 857
WARNING: Too many unnamed arguments supplied, in file GDMUtils.scad, line 857
WARNING: variable l not specified as parameter, in file cable_chain_mount_parts.scad, line 123
./stl_normalize.py -c STLs/cable_chain_mount_parts.stl -o STLs/cable_chain_mount_parts.stl
/Applications/OpenSCAD.app/Contents/MacOS/OpenSCAD -m make -o STLs/compression_screw_parts.stl compression_screw_parts.scad
WARNING: rx was assigned on line 402 of "GDMUtils.scad" but was overwritten on line 404
WARNING: ry was assigned on line 403 of "GDMUtils.scad" but was overwritten on line 405
./stl_normalize.py -c STLs/compression_screw_parts.stl -o STLs/compression_screw_parts.stl
/Applications/OpenSCAD.app/Contents/MacOS/OpenSCAD -m make -o STLs/cooling_fan_shroud_parts.stl cooling_fan_shroud_parts.scad
WARNING: rx was assigned on line 402 of "GDMUtils.scad" but was overwritten on line 404
WARNING: ry was assigned on line 403 of "GDMUtils.scad" but was overwritten on line 405
WARNING: Ignoring unknown variable '$do_prerender', in file GDMUtils.scad, line 7.
WARNING: variable center not specified as parameter, in file GDMUtils.scad, line 914
WARNING: variable center not specified as parameter, in file GDMUtils.scad, line 915
WARNING: variable center not specified as parameter, in file GDMUtils.scad, line 918
WARNING: variable center not specified as parameter, in file GDMUtils.scad, line 919
./stl_normalize.py -c STLs/cooling_fan_shroud_parts.stl -o STLs/cooling_fan_shroud_parts.stl
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
buddybu, 2020-06-04:
I am seeing this same error.  Help?

dsbaars, 2020-08-26:
Same here, compiling manually in the OpenSCAD gui does work. It is the "stl_normalize.py" script that generates errors. I tried commenting out the drive_gear_parts and xy_sled_parts to make the rest compile, since I only need the glass and heated bed clips changed and those throw errors but somehow that does not fix it.

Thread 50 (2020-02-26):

Power delivery questions

Ian-Korob, 2020-02-26:
stupid question: Does the power supply shown in the BOM plug into the arduino or do you strip it and put it into the other board? Also how does the other board go into the arduino, is it like a shield that slots into the pins? Thanks, this was my one concern before starting.

bthayer3, 2020-02-27:
The power supply plugs into the Ramps board, the Arduino gets power through the Ramps board. Checkout the wiring diagram picture at the bottom of the page [here.](https://github.com/revarbat/snappy-reprap/wiki/v3.0-Assembly) The Ramps board goes on top of the Arduino, it is a shield. It you line Ramps board on top of the Arduino, you will notice the pins match the corresponding slots on the Arduino. Also, don't be afraid to do extra research when building yours as there is plenty of other tutorials done by people who use the Ramps board to build their own 3D printers; they definitely help explain extra details and configurations.

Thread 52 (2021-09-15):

Material Recommendations

ulrichsc, 2021-09-15:
Are there any recommendations which part to print with which filament type?
My considerations so far are to use PLA or PETG for the larger body parts (cheap, less bending). For the mechanical parts (gears etc.) I consider using CPE or ABS.

revarbat, 2021-09-16:
I printed it all in PLA. I just used high infill % for the drive gears and small extruder parts.

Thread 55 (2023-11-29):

Slop Calibrator plug doesn't fit

sailor-vhs, 2023-11-29:
Hi! I started the process of printing snappy 3.0. Printed the slop calibrator but the plug doesn't fit in any hole.

I'm using a Creality CR-10S PRO V2

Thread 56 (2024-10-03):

3MF files

NicholasParry, 2024-10-03:
Could someone export 3mf files for me, im struggling to get opens cad to play nice.

NicholasParry, 2024-10-03:
Meant to say step files not 3mf. What I’m wanting to do is bring the model into fusion.

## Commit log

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2014-08-30 Split NEMA modules out of GDMUtils.scad. Split T-slot modules out of joiners.scad.
    [GDMUtils.scad, NEMA.scad, cap_parts.scad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]
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2014-08-31 Fixed up thinning_wall issues.
    [GDMUtils.scad, config.scad, drive_gear_parts.scad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]
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2014-08-31 Added Nut holder to Z-sled. Tweaked rollers to reduce friction.
    [cap_parts.scad, config.scad, drive_gear_parts.scad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]
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2014-09-01 Fixed lifter hex nut size for Z-axis sled.
    [slider_sled.scad]
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2014-09-01 Added extruder platform. Color coded parts for rendering.
    [GDMUtils.scad, cap_parts.scad, config.scad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]
2014-09-01 Tightened up tolerances for rollers and captured lister nuts.
    [roller_parts.scad, slider_sled.scad, z_sled_part.scad]
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2014-09-03 Refactored nut capture assembly into it's own module file.
    [capture_nut_cap.scad, config.scad, nut_capture.scad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]
2014-09-04 Added tolerances test calibration plate.
    [test_part.scad, tolerances_test_part.scad]
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2014-09-04 Fixed some part names,
    [lifter_rod_coupler_part.scad]
2014-09-04 Fixed for renames.
    [full_assembly.scad, slider_sled.scad]
2014-09-04 Made printed acme threaded nuts into cartridges for nut capture housing.
    [acme_screw.scad, lifter_nut_part.scad, tolerances_test_part.scad]
2014-09-04 Fixed up wiring access holes.
    [rail_with_motor_mount_part.scad, yz_joiner_part.scad]
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2014-09-05 Increased size of lifter nut snaps ridges.
    [lifter_nut_part.scad, nut_capture.scad]
2014-09-05 Tightened up roller caps. Added lifter nuts to full assembly model.
    [full_assembly.scad, lifter_nut_part.scad, roller_cap_parts.scad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]
2014-09-06 Simplified code for making snap-tab joiner pairs and quads.
    [full_assembly.scad, joiners.scad, motor_mount_plate_parts.scad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]
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2014-09-10 Centralized slop setting, and improved slop calibration model.
    [acme_screw.scad, config.scad, drive_gear_parts.scad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]
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2014-09-12 Updated motor shaft slop.
    [drive_gear_parts.scad, drive_gear_parts.stl, lifter_rod_coupler_parts.scad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]
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2014-09-29 Added half_joiner modules. Refactored joiners to be made from half_joiners.
    [config.scad, full_assembly.scad, joiners.scad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]
2014-10-04 Lowered cantilever. Moved XY endstops. Added build style options. Centered extruder platform. Changed rail side mounts to half-joiners. Squared slop calibration Parts.
    [GDMUtils.scad, NEMA.scad, cantilever_joint_parts.scad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]
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2014-10-07 Rotate extruder platform to have consistent long axis with every other part.
    [extruder_platform_parts.scad, extruder_platform_parts.stl]
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2014-10-08 Blunted corners on, added wiring holes to, and added z-endstop adjustment to the extruder platform.
    [GDMUtils.scad, cantilever_arm_parts.scad, cantilever_arm_parts.stl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]
2014-10-08 Chamferred extruder platform corners. Rounded motor mount corners.
    [extruder_platform_parts.scad, extruder_platform_parts.stl, motor_mount_plate_parts.scad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]
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2014-10-19 Added bracing to extruder platform, and endstop standoffs.
    [GDMUtils.scad, cantilever_arm_parts.scad, cantilever_arm_parts.stl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]
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2014-10-29 Fixed various joiner clearance issues. Cleaned up rails.
    [cable_chain_link_parts.stl, cantilever_arm_parts.scad, cantilever_arm_parts.stl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]
2014-11-02 Moved from lifter screw to geared Z axis. Improved grid_of(). Added chamfer().
    [GDMUtils.scad, cable_chain_link_parts.stl, cantilever_arm_parts.stl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]
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2014-11-06 Contraction strain relief. Double-sided rail for future slider mods.
    [rail_motor_segment_parts.scad, rail_motor_segment_parts.stl]
2014-11-07 Merged slider_sled.scad and sled_parts.scad. Preliminary changes towards XY sled animations.
    [GDMUtils.scad, cantilever_arm_parts.stl, cantilever_joint_parts.stl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]
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2014-11-08 Fixed manifold issues with newer OpenSCAD.
    [cable_chain_link_parts.stl, cantilever_arm_parts.scad, cantilever_arm_parts.stl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]
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2014-11-12 Merged slider_sled.scad and sled_parts.scad. Added chamfers to rail ends.
    [cable_chain_link_parts.stl, rail_motor_segment_parts.scad, rail_motor_segment_parts.stl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]
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2014-11-20 Shrinkage relief for more parts. Fan shroud more integrated.
    [build_platform_support_parts.stl, cable_chain_link_parts.stl, cantilever_arm_parts.scad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]
2014-11-20 Fixed rendering errors with extruder platform and fan shroud.
    [build_platform_support_parts.stl, cable_chain_link_parts.stl, cantilever_arm_parts.stl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]
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2014-11-24 Added cable chain joiners. Shortened some parts names.
    [cable_chain_link_parts.scad, cable_chain_link_parts.stl, cable_chain_parts.scad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]
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2015-02-09 Fixed positioning of extruder platform in full rendering.
    [full_assembly.scad]
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2015-02-12 Tweaked nut capture holes on lifter rod coupler.
    [lifter_rod_coupler_parts.scad, lifter_rod_coupler_parts.stl]
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2015-02-17 Fixed rendering of joiner.
    [cantilever_joint_parts.scad]
2015-06-18 Improved Z axis with much less wobble.
    [GDMUtils.scad, cable_chain_link_parts.stl, cable_chain_mount_parts.stl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]
2015-06-19 Tweaked z platform to me more easily printable.
    [cable_chain_link_parts.stl, cable_chain_mount_parts.stl, config.scad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]
2015-06-20 Fixed platform width.
    [cable_chain_link_parts.stl, cable_chain_mount_parts.stl, config.scad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]
2015-06-21 Removed rail from bridge. Added wiring access holes.
    [bridge_center_parts.scad, bridge_center_parts.stl, bridge_segment_parts.scad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]
2015-06-23 Updated cable chain anchors. Redesigned Z sled.
    [cable_chain_link_parts.scad, cable_chain_link_parts.stl, cable_chain_mount_parts.scad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]
2015-06-24 Fixed up cable chain mounts. Fixed lifter couplers.
    [cable_chain_mount_parts.scad, cable_chain_mount_parts.stl, lifter_rod_coupler_parts.scad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]
2015-06-24 Added wiring access holes to xy_joiner. Added flattened shaft support to lifter_connector.
    [drive_gear_parts.scad, drive_gear_parts.stl, lifter_rod_coupler_parts.scad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]
2015-06-24 Fix non-manifold issues.
    [extruder_platform_parts.scad, extruder_platform_parts.stl]
2015-06-26 Fixed non-manifold issues with motor mount plate.
    [motor_mount_plate_parts.scad, motor_mount_plate_parts.stl]
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2015-07-03 Smoothed platform slider ridge. Added limit switch mounts on rail endcap.
    [cable_chain_link_parts.stl, cable_chain_mount_parts.stl, drive_gear_parts.stl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]
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2015-07-05 Refactored full_assembly module to allow for future assembly instruction generation.
    [config.scad, full_assembly.scad]
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2015-07-07 Allow for slop on motor mount.
    [NEMA.scad, drive_gear_parts.scad, drive_gear_parts.stl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]
2015-07-08 Added optional sidewars mount orientation to extruder platform.
    [extruder_platform_parts.scad, extruder_platform_parts.stl]
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2015-07-10 Added lifter lock nuts. Tweaked acme threaded rod thread profile.
    [acme_screw.scad, cable_chain_link_parts.stl, cable_chain_mount_parts.stl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]
2015-07-10 Changed half joiner orientations to make it more flexible for cable chain placement.
    [cable_chain_mount_parts.scad, cable_chain_mount_parts.stl, rail_xy_motor_segment_parts.scad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]
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2015-07-21 Tighten up NEMA motor mounts.
    [filament_hanger_parts.scad, filament_hanger_parts.stl, motor_mount_plate_parts.scad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]
2015-07-21 Make Acme threadings default to tighter thread angle.
    [acme_screw.scad]
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2015-08-05 Fixed full rendering.
    [extruder_idler_parts.scad, extruder_idler_parts.stl]
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2015-08-25 Shortened extruder platform. Tweaked spool holder. Reduced facet counts. Moved side joiners to rail segments from motor segments.
    [cable_chain_link_parts.stl, cable_chain_mount_parts.scad, cable_chain_mount_parts.stl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]
2015-08-26 Corrected rack-and-pinion tolerances.
    [cable_chain_link_parts.stl, cable_chain_mount_parts.stl, config.scad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]
2015-09-07 Remove modules not needed for direct drive z axis.
    [lifter_lock_nut_parts.scad, lifter_rod_coupler_parts.scad, rail_xy_motor_segment_parts.scad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]
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2015-09-08 Bevelled sliders. Renamed xy_sled to xy_sled. Upped csglimit.
    [full_assembly.scad, sled_parts.scad, sled_parts.stl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]
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2015-09-10 Fixed revision number to v1.0.
    [config.scad]
2015-09-10 Adjusted rail slider slop.
    [sled_parts.scad]
2015-09-10 re-adjusted rail slop.
    [sled_parts.scad]
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2015-09-10 Corrected sled endcap parts count in model.
    [sled_endcap_parts.scad, sled_endcap_parts.stl]
2015-09-14 Fixed spool holder flaw.
    [config.scad, spool_holder_parts.scad, spool_holder_parts.stl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]
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2015-09-14 Corrected cable chain mounts for the move of side joiners from motor rails to rail segments.
    [cable_chain_mount_parts.scad, cable_chain_mount_parts.stl]
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2015-09-17 Loosened sliders slightly.
    [cooling_fan_shroud_parts.stl, sled_parts.scad, sled_parts.stl]
2015-09-17 Changed motor mount plate from 2x2 to single part.
    [motor_mount_plate_parts.scad, motor_mount_plate_parts.stl]
2015-09-18 Reduced parts sizes to be printable in a 150x150mm area.
    [config.scad, extruder_fan_shroud_parts.stl, jhead_platform_parts.stl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]
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2015-09-18 Added STL for Reduced cable chain link footprint.
    [cable_chain_link_parts.stl]
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2015-09-18 Fixed up rail_motor_segment bottom crossbracing to be less bizarre.
    [rail_motor_segment_parts.scad, rail_motor_segment_parts.stl]
2015-09-22 Replace expensive slot hulls with simple cylinder-cube-cylinder unions.
    [GDMUtils.scad, jhead_platform_parts.scad]
2015-09-22 Make rail segments symmetrical, because I keep putting them together backwards!
    [rail_segment_parts.scad]
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2015-09-23 Thickened xy joiner to make the rack hardstop sturdier.
    [cooling_fan_shroud_parts.stl, xy_joiner_parts.scad, xy_joiner_parts.stl]
2015-09-27 Revarted to lifter rods for the Z axis.
    [config.scad, cooling_fan_shroud_parts.stl, drive_gear_parts.scad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]
2015-09-27 Fixed issue #3: YZ Joiner cable hole problem with crossbeam style walls
    [yz_joiner_parts.scad]
2015-09-28 Tighten up extruder latch. Loosen z_sled threaded rod clamp slightly.
    [extruder_idler_parts.scad, extruder_idler_parts.stl, z_sled_parts.scad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]
2015-09-28 Fixed issue #5: wiring access holes not needed with crossbeam wall styles.
    [rail_segment_parts.scad, rail_xy_motor_segment_parts.scad, rail_z_motor_segment_parts.scad]
2015-09-28 Added generated parts for wiring access hole fixes.
    [rail_xy_motor_segment_parts.stl, rail_z_motor_segment_parts.stl]
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2015-10-10 Added diffs file for Marlin/RAMPS firmware for Snappy.
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2015-10-12 Removed limit switch clip from Y axis endcaps.
    [full_assembly.scad, rail_y_endcap_parts.scad, rail_y_endcap_parts.stl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]
2015-10-15 Fixed issue #6: Wiring access holes need frames on corrugated walls.
    [rail_segment_parts.scad, rail_xy_motor_segment_parts.scad, rail_z_motor_segment_parts.scad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]
2015-10-19 Fixed verbosity bug. Added binary stl write option.
2015-10-26 Added gear_backlash config. Corrected drive gear helical angle.
    [config.scad, drive_gear_parts.scad, drive_gear_parts.stl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]
2015-11-01 Removed redundant slop offset for XY sled rack.
    [drive_gear_parts.scad, drive_gear_parts.stl, rail_segment_parts.stl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]
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2016-06-19 Fix rendering.
    [full_assembly.scad]
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2017-03-30 Fixed non-manifold issues. Regenerated STLs.
    [cooling_fan_shroud_parts.stl, drive_gear_parts.stl, extruder_fan_shroud_parts.stl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]
2017-03-30 Fixed Assembly instructions markdown formatting.
2017-04-01 First pass update of assembly docs. Some manifold fixes.
    [config.scad, full_assembly.scad, jhead_platform_parts.stl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]
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2017-04-02 Fixed v1.5 Assembly docs image links.
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2017-04-05 Fixed overhang issues with Z sled.
    [z_sled_parts.scad, z_sled_parts.stl]
2017-04-08 Lengthened lifter screw to reduce wobble.
    [config.scad, jhead_platform_parts.stl, lifter_screw_parts.stl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]
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2017-04-25 Redesigned Z axis to fix lifter binding issues.
    [GDMUtils.scad, bridge_segment_parts.scad, bridge_segment_parts.stl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]
2017-04-29 Added adjustable bed mounts. Replaced extruder latch with compression screw.
    [GDMUtils.scad, adjustment_screw_parts.scad, adjustment_screw_parts.stl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]
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2017-04-30 Fixed arrow placement for final_assembly_6.
    [full_assembly.scad]
2017-05-01 Fixed blockage in bridge side joiner.
    [bridge_segment_parts.scad, bridge_segment_parts.stl]
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2017-05-03 Reduced some non-manifold issues. Added Snappy placard.
    [adjustment_screw_parts.stl, bridge_segment_parts.stl, cable_chain_link_parts.stl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]
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2017-05-04 Fixed rack shape calculation. Widened drive gear.
    [config.scad, drive_gear_parts.scad, drive_gear_parts.stl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]
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2017-05-13 Fixed several polyhedron face orientation errors.
    [GDMUtils.scad]
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2017-05-14 Added bracing on sled endstops to prevent flexing.
    [full_assembly.scad, sled_endcap_parts.scad, sled_endcap_parts.stl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]
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2017-05-16 Fixed issue with jhead platform side joiners.
    [jhead_platform_parts.scad, jhead_platform_parts.stl, snappy_logo_parts.scad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]
2017-11-11 Fixed Z-sled clearance against Z-rail.
    [ramps_mount_parts.stl, z_rail_parts.scad, z_rail_parts.stl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]
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2017-11-21 Made set screw nut less likely to rotate freely in drive gears.
    [drive_gear_parts.scad]
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2018-01-10 Initial Snappy3 redesign.
    [GDMUtils.scad, bridge_segment_parts.scad, bridge_segment_parts.stl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]
2018-01-10 Fixed non-manifold bridge segment model.
    [bridge_segment_parts.stl]
2018-01-10 Fixed logo placard text.
    [snappy_logo_parts.scad, snappy_logo_parts.stl]
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2019-02-17 Update README.md
    describe printer slop process
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
